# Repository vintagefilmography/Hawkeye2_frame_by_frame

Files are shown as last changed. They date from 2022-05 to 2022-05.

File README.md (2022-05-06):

# Hawkeye2_frame_by_frame
The purpose of this project is to prvide the instruction to the user on how to modify the existing 8mm film projector for the frame-byframe capture directly into the camera using a small MSP430 based board.  
Generally the projects of this type require several modifications to the projector including the light change, motor change and addition of some type of a trigger detector for the camera.  
This project also requires the light change and the motor change, but unlike similar other projects, it does not require the trigger mechanism. The trigger is pprovided by the MSP430 controller. The controller is programmed to precisely control the stepper motor rotation so that the film gets advanced exactly one frame at the time. The camera trigger is then generated at the end of frame advance.  

System Components



## Hawkeye2 Controller  
At the heart of the system is the Hawkeye2 controller. This is a custom design. All design info is available gere is this repository. The board details are included in  the homemade-v3 folder. Download the folder to your Eagle project directory and there you will have access to the schematic and the board layout. 
The MSP430 micro controller firmware is available in the MSP folder. Download the zip file from there and save it in you TI Code Composer project directory. From there you can edit the source and flash the target by using TI Launchpad.  
There are two more boards included. One is for the front panel switches and the other is for the switch interface board. Follow the included wiring diagram to interconnect the system.
## Stepper Driver  
The stepper driver is an off the shelf product. 
https://www.amazon.com/gp/product/B075HBJP51/
There are many other variants available. This particular one is a good choice because it has 256 micro steps allowing for a very precise tuning control. One disadvantage is that it operates from a 24VDC source so that 2 DC adaprers are required, one for the driver and the other one for the controller that requires 12VDC source.  
Driver dip switches  
The following is recommended:
SW4 - Half Currect
Current - 
1.4A for this type motor https://www.amazon.com/gp/product/B00PNEQKC0/
2.7A for this type motor https://www.amazon.com/gp/product/B00PNEPF5I/
Set the pulse/rev switches for the highest speed that can still hold the torque and there is no skipping of steps. Skipping will result in loss of synchronization.  
## Stepper Motor  
These two motors were tested.
1.4A for this type motor https://www.amazon.com/gp/product/B00PNEQKCdesigned with Spark0/
2.7A for this type motor https://www.amazon.com/gp/product/B00PNEPF5I/
You will have to design a bracket for the motor so that it fits properly in the projector after you remove the old motor. 
A sample stepper bracket is included here as a good staring point. Use the Designspark Mechanical free software to modify the bracket for your projector.

## Pulley
There are quite a few pulleys avaliable online.  
Example:  
https://www.amazon.com/gp/product/B07C4R3PGV/  
https://www.amazon.com/gp/product/B07C4QD1BV/
You can also design your own. A sample design will be included here shortly.

## Belt
This used to be a big problem but with the neophrene Urethane belting that became available it is easy to make your own custom belt.
https://www.amazon.com/gp/product/B07L3W7Z1N  
Follow the following instructions:  
https://www.youtube.com/watch?v=mBtHvPWVgDw

## Control Switches:

front_panel

The control switches control the operation of the unit.  
### RUN Switch
Pauses the operation  
### ALIGN
Slowly advances the film until the frame is centered in the camera. Also turns tuning on if activated in run mode.  
### REW
Turns takeup continuously on if run switch is off.  
The switch can also be used in conjuction with the PROJ switch to select the projector type. 
I.e. if the setup is used with multiple projectors then the projector synchronization can be saved in non volatile memory.  
Four memory locations are available:   
REW     PROJ  
0       0       Projector1  
0       1       Projector2  
1       0       Projector3  
1       1       Projector4  
The switches are active only during a short time after the power is plugged in and in most cases the only Projector1 selection will be used.  

### PROJ 
Seects the projector type used. In most cases this switch will be kept off. 
The projector selection is read by the firmware upon board power up and cannot be changed after that during normal operation.  
### UP and DOWN switches 
Used during tuning mode to run change the length of stepper advance.  
### Up and DOWN buttons
Located on the controller board, used for fine tuning of the stepper  
### REV Switch 
Reverses the motor rotation for film rewind.  

## Operation
Very straight forward. Here is a short video showing the operation.  
https://photos.app.goo.gl/MLEgviiinpVREHCQA  
As the video shows, plug the power in for both the controller and the driver and then flip the ADV switch on until the projector is finished with the film frame advance and at that point turn the ADV switch off. Then, connect the camera trigger and turn the camera on. Turn the RUn switch on the the camera will start capturing the farmes. If at any point the system starts goung out of sync you can resync it by using the ADV switch or alternatively, turn the ALG switch on and the hit the UP or DOWN button just once.   
The UP button makes the run shorter and the DOWN button makes it longer.  

## Tuning the Stepper  
Turn the RUN switch on. Make sure all other switches are off.


Turn the ALIGN switch on.  
This puts the controller into tuning mode.  
Turn on the DOWN switch. This makes the stepper step one count longer.  
While the DOWN switch is still on, turn on the UP switch.  
This will cause continuous stepper count increase. You will see that the film advance becomes larger and larger.   
After a while the stepper motor advance will  be close to one full turn of the projector cam.  
Once the alignment is close to a full cam rotation, turn the UP switch off and then the DOWN switch off.   
Continue with fine tuning by using the controller board mounted UP and DOWN buttons.  
The UP button will make the advance shorter by one count and conversely, the DOWN button will make it longer by one count.  
Once the alignment is done DO NOT POWER THE BOARD DOWN.  
Turn the ALIGN switch off and then the RUN switch off. Then you can power the board down.  
Power the board up again with the correct memory selected.
Turn the RUN switch on and check that the alignment was restored properly from the memory.  
It is to be noted that the UP and DOWN sequence can be reversed if the Film advance is too large.  
In that case turn the UP switch on first followed by the DOWN switch.   
Once done, turn the DOWN switch off first followed by the UP switch.

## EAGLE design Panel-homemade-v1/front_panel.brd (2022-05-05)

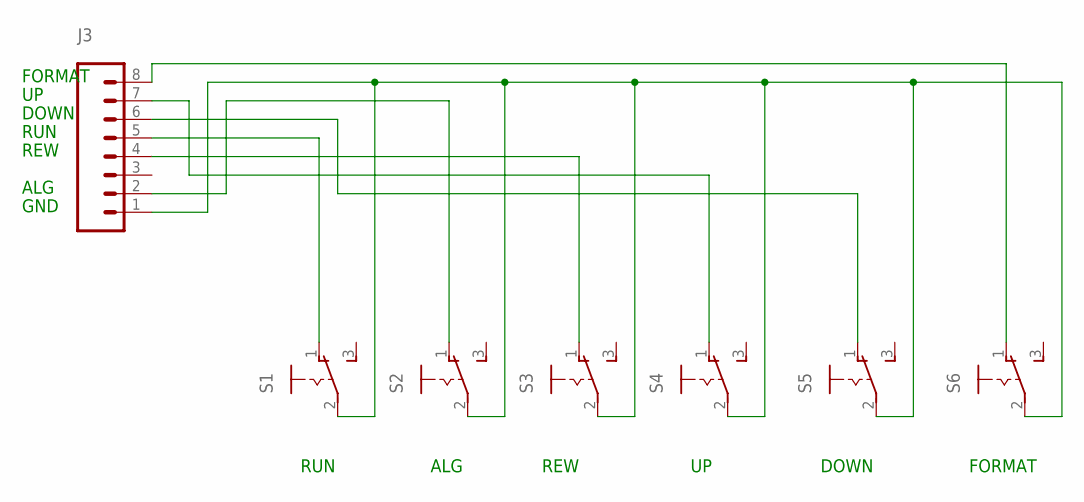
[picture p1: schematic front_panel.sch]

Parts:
J3: CONN_08"; 1X08
S1, S2, S3, S4, S5, S6: M251

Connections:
unnamed: J3.1, S1.2, S2.2, S3.2, S4.2, S5.2, S6.2
unnamed: J3.6, S5.1 (O)
unnamed: J3.4, S3.1 (O)
unnamed: J3.7, S4.1 (O)
unnamed: J3.2, S2.1 (O)
unnamed: J3.5, S1.1 (O)
unnamed: J3.8, S6.1 (O)

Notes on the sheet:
GND
ALG
REW
RUN
DOWN
FORMAT

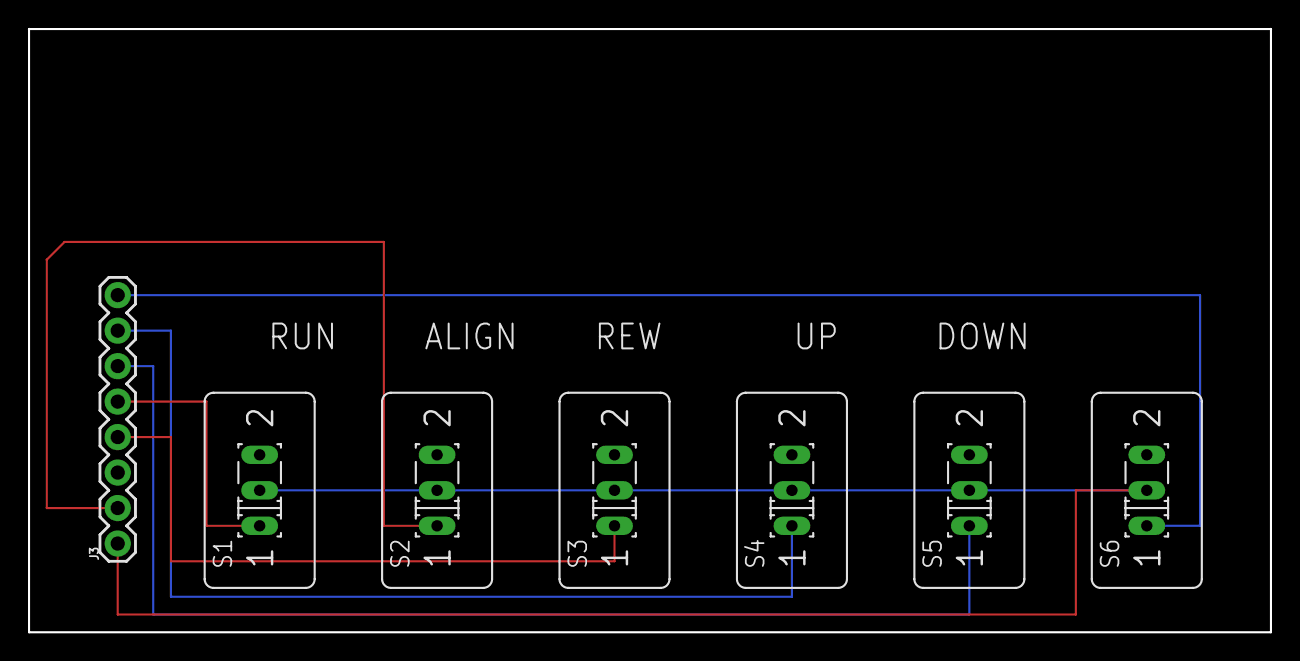
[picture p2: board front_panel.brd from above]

Board: 2 copper layers, 88.9 x 43.2 mm, 7 parts (0 on the bottom side), 7 nets.

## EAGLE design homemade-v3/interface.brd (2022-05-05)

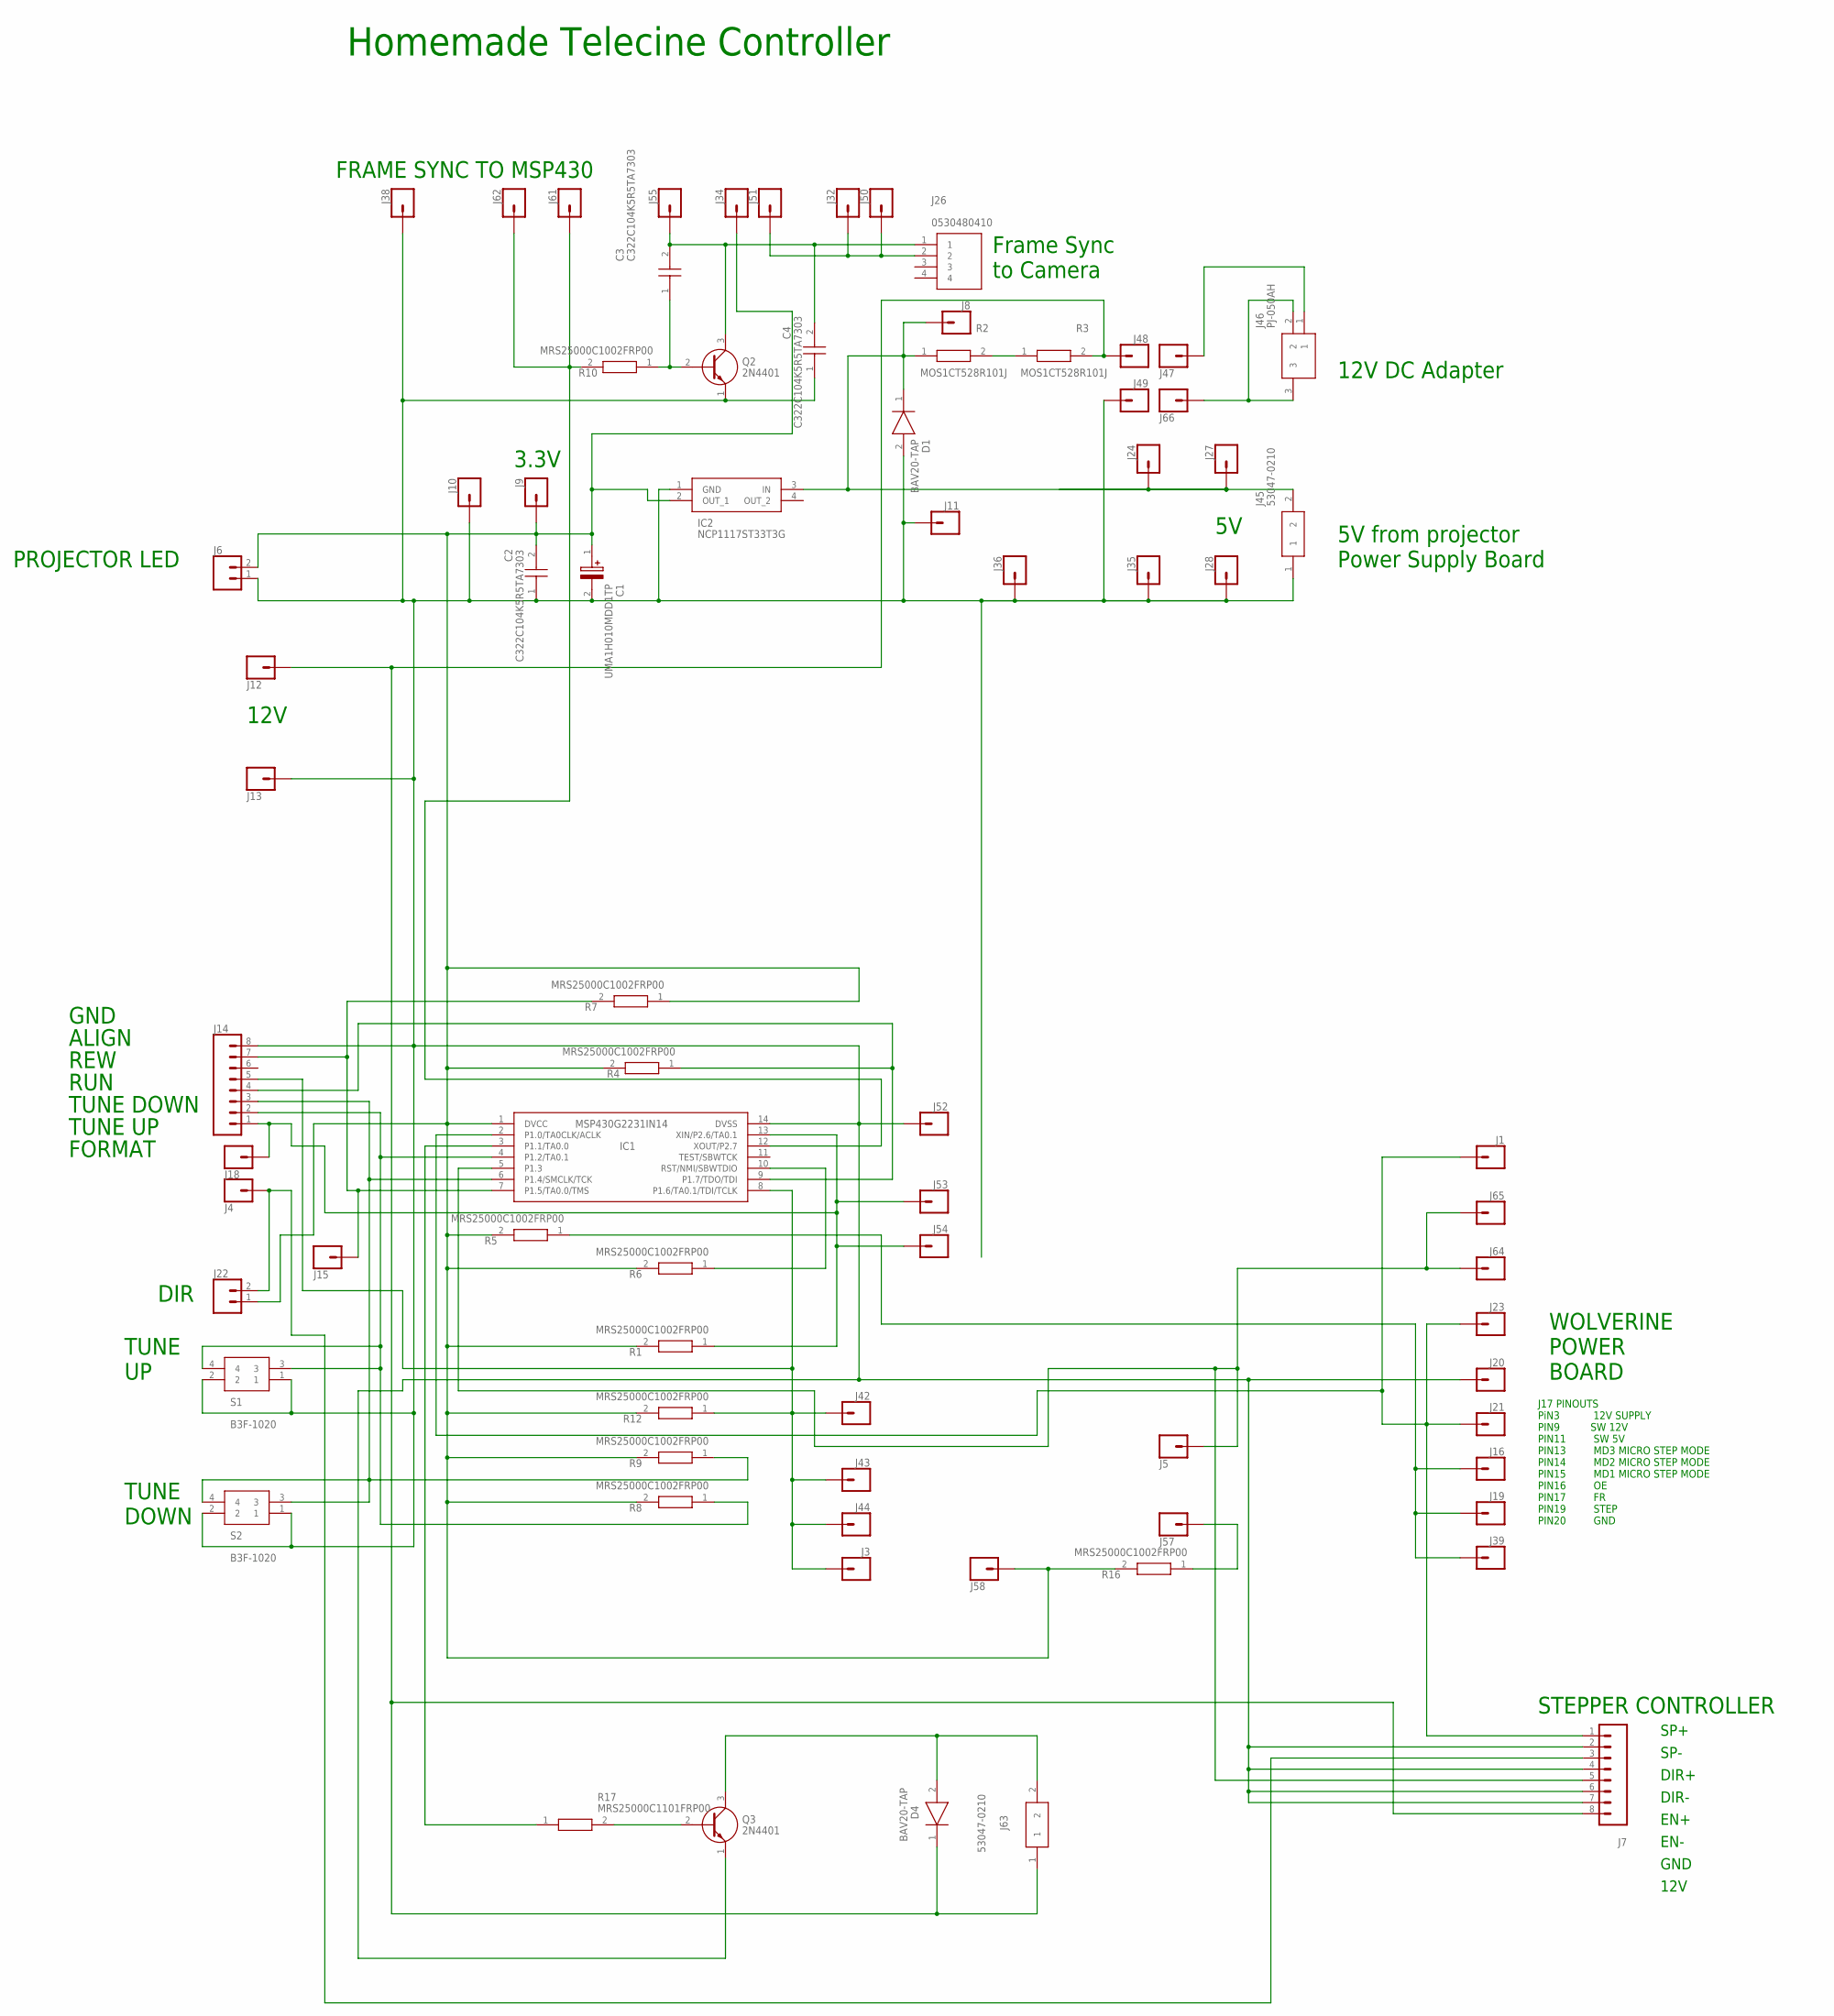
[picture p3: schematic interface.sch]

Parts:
C1: UMA1H010MDD1TP; CAPPRD150W45D450H600
C2, C3, C4: C322C104K5R5TA7303; C322
D1, D4: BAV20-TAP; DIOAD950W60L350D150
IC1: MSP430G2231IN14; DIP254P762X508-14
IC2: NCP1117ST33T3G; SOT230P700X180-4N
J1, J3, J4, J5, J8, J9, J10, J11, J12, J13, J15, J16, J18, J19, J20, J21, J23, J24, J27, J28, J32, J34, J35, J36, J38, J39, J42, J43, J44, J47, J48, J49, J50, J51, J52, J53, J54, J55, J57, J58, J61, J62, J64, J65, J66: CONN_01; 1X01
J6, J22: CONN_02; 1X02
J7, J14: CONN_08"; 1X08
J26: 0530480410; SHDR4W35P0X125_1X4_675X550X350
J45, J63: 53047-0210
J46: PJ-050AH; PJ050AH
Q2, Q3: 2N4401; CS_TO-92
R1, R4, R5, R6, R7, R8, R9, R10, R12, R16: MRS25000C1002FRP00; RESAD1650W60L650D250
R2, R3: MOS1CT528R101J; RESAD2100W60L900D300
R17: MRS25000C1101FRP00; RESAD1650W60L650D250
S1, S2: B3F-1020; B3F1000

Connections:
unnamed: C3.2, C4.2, J26.1, J55.1, Q2.3 (C)
unnamed: IC1.13 (XIN/P2.6/TA0.1), J14.1, J18.1, J53.1, J54.1, R1.1
unnamed: D4.1 (K), J7.8, J12.1, J48.1, J63.1, R3.2
unnamed: IC1.9 (P1.7/TDO/TDI), J14.4, R4.1
unnamed: J57.1, R16.1
unnamed: C1.1 (+), C2.2, IC1.1 (DVCC), IC2.2 (OUT_1), J6.2, J9.1, J22.1, J34.1, J58.1, R1.2, R4.2, R5.2, R6.2, R7.1, R8.2, R9.2, R12.2, R16.2
unnamed: IC1.3 (P1.1/TA0.0), R17.1
unnamed: IC1.10 (RST/NMI/SBWTDIO), R6.1
unnamed: R2.2, R3.1
unnamed: J4.1, J7.3, J22.2
unnamed: D1.1 (K), IC2.3 (IN), J8.1, J24.1, J27.1, J45.2, R2.1
unnamed: J46.1, J47.1
unnamed: IC1.7 (P1.5/TA0.0/TMS), J14.7, J15.1, R7.2
unnamed: J16.1, J19.1, J39.1, R5.1
unnamed: IC1.5 (P1.3), J5.1, J7.5, J64.1, J65.1
unnamed: IC1.2 (P1.0/TA0CLK/ACLK), J1.1, J7.1, J21.1, J23.1
unnamed: IC1.4 (P1.2/TA0.1), J14.2, R8.1, S1.3, S1.4
unnamed: C1.2 (-), C2.1, C4.1, D1.2 (A), IC1.14 (DVSS), IC2.1 (GND), J6.1, J7.2, J7.4, J7.6, J7.7, J10.1, J11.1, J13.1, J14.8, J20.1, J28.1, J35.1, J36.1, J38.1, J45.1, J49.1, J52.1, Q2.1 (E), Q3.1 (E), S1.1, S1.2, S2.1, S2.2
unnamed: IC1.6 (P1.4/SMCLK/TCK), J14.3, R9.1, S2.3, S2.4
unnamed: IC1.12 (XOUT/P2.7), J61.1, J62.1, R10.2
unnamed: Q3.2 (B), R17.2
unnamed: C3.1, Q2.2 (B), R10.1
unnamed: J26.2, J32.1, J50.1, J51.1
unnamed: IC1.8 (P1.6/TA0.1/TDI/TCLK), J3.1, J14.5, J42.1, J43.1, J44.1, R12.1
unnamed: J46.2, J46.3, J66.1
unnamed: D4.2 (A), J63.2, Q3.3 (C)

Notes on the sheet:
Homemade Telecine Controller
PROJECTOR LED
3.3V
FRAME SYNC TO MSP430
Frame Sync to Camera
5V from projector Power Supply Board
12V
RUN
ALIGN
WOLVERINE POWER BOARD
J17 PINOUTS PiN3 12V SUPPLY PIN9 SW 12V PIN11 SW 5V PIN13 MD3 MICRO STEP MODE PIN14 MD2 MICRO STEP MODE PIN15 MD1 MICRO STEP MODE PIN16 OE PIN17 FR PIN19 STEP PIN20 GND
12V DC Adapter
SP-
STEPPER CONTROLLER
SP+
EN-
EN+
DIR-
DIR+
GND
REW
DIR
TUNE UP
TUNE DOWN
TUNE DOWN
TUNE UP
FORMAT

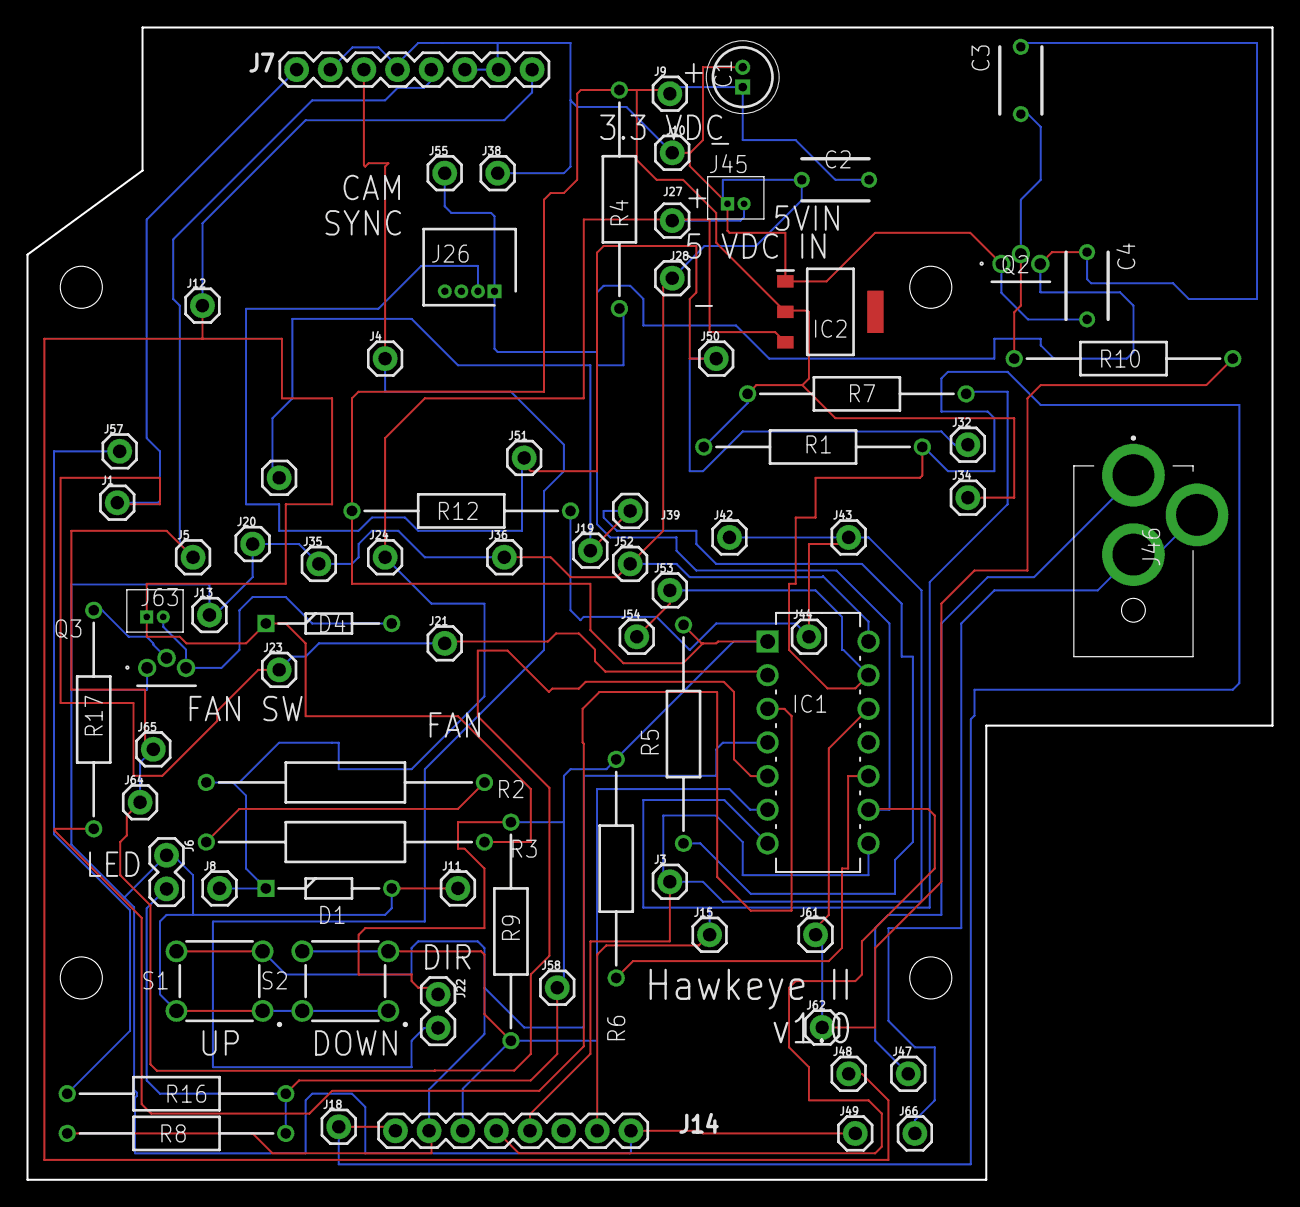
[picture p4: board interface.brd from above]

Board: 2 copper layers, 94.0 x 87.0 mm, 78 parts (0 on the bottom side), 26 nets.

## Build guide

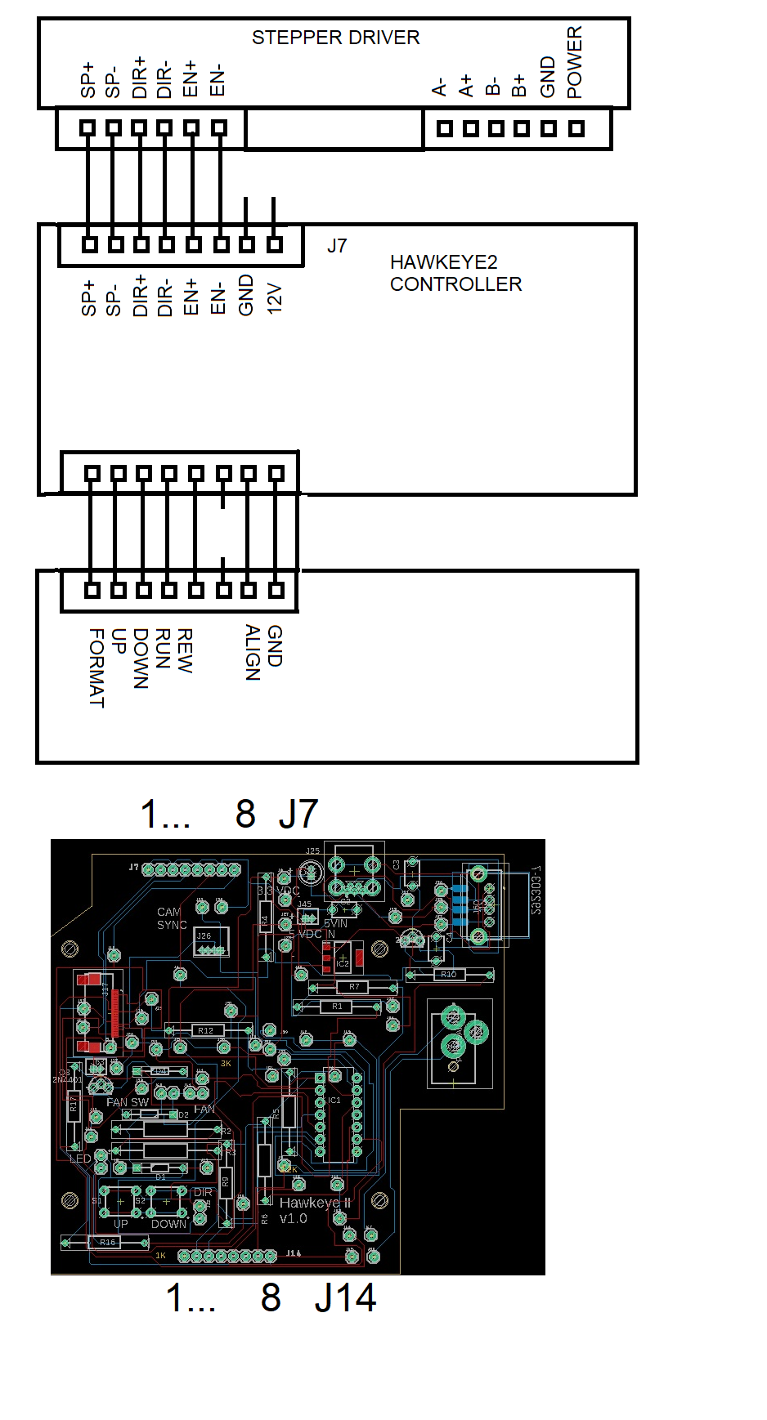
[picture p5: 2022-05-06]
wiring-V3.png

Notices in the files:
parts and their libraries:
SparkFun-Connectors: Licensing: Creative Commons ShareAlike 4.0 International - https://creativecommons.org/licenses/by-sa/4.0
